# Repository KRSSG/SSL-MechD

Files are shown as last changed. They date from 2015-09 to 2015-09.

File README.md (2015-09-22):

# SSL-MechD
Mechanical Design of Robocup SSL Robots designed by KRSSG, IIT Kharagpur

##SSL v1.0

##SSL v2.0

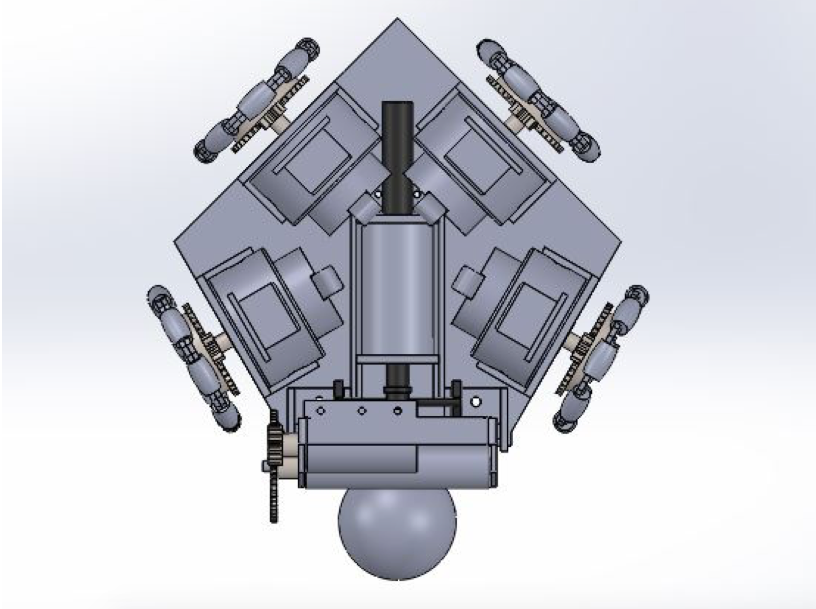
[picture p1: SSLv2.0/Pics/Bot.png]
SSL v2.0


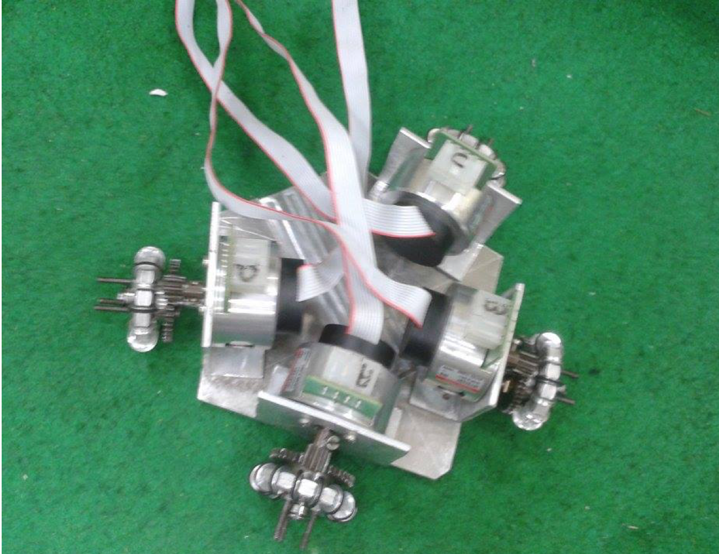
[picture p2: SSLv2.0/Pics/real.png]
SSL Robot


###Locomotion System
The locomotion system is a four wheel drive with 2 wheels inclined at 90° and the other two inclined at 120° to provide space for dribbler and kicker mechanism. The bot has a single centre of rotation and it comes well within the 18 cm diameter following the rules of Small Sized League Robocup competition (SSL). 
#####Wheels
Omni wheels are used which can move in either direction. There are 8 small sub wheels which allows the wheel to move perpendicularly.
#####Gears
Spur gears are used between wheels and motors. 
#####Motors
The motor used for driving is Maxon EC 45.

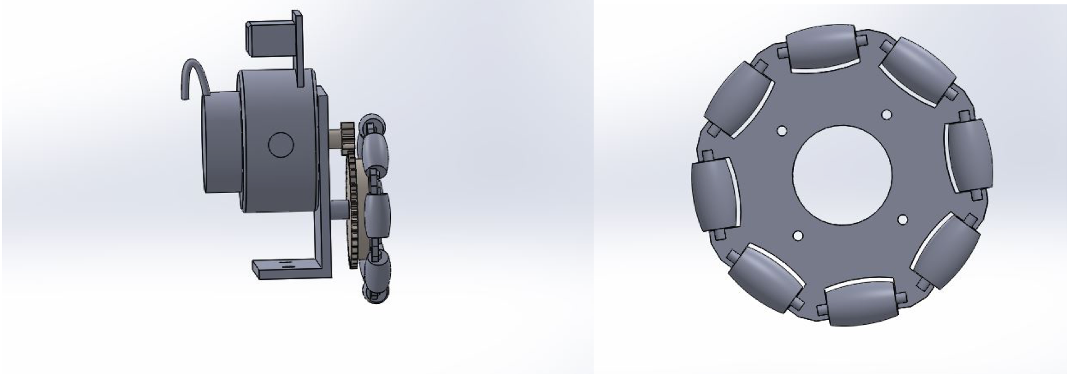
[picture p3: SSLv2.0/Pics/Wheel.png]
Wheel


###Dribbling Mechanism

A circular dribbler made of Aluminium is used. Dribbler bar is directly driven by a brushless Maxon EC16 (16W) motor through the gears with a gear ratio of 4:1. 
To stop the ball from recoiling on impact spring is used to dissipate its kinetic energy to ensure a maximum of ball handling. Further, rubber pad will be used as dampener.
 
According to the rules, geometrical design of this system is in a way that it should not consist more than 20% of the ball. Furthermore, the ball should stick entirely to the robot during the movement. So our Dribbler holds up to 20% of the ball when receiving a pass, and somewhat less than when the ball is at rest or during normal dribbling.

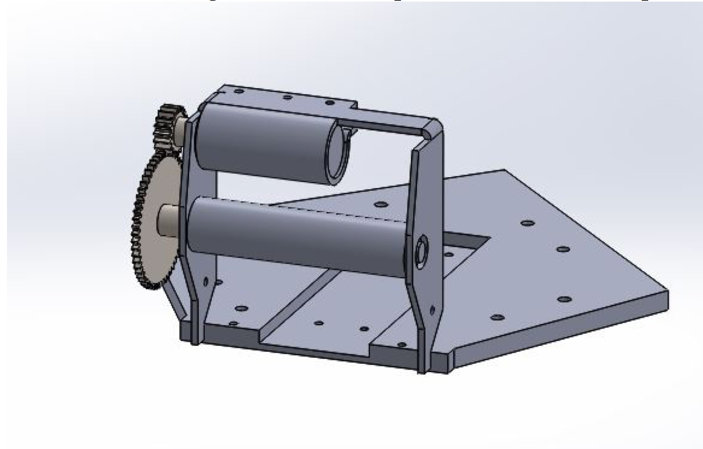
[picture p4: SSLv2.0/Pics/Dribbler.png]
Dribbler


###Kicker System
The shooting mechanism is works on the principle of inductive resistance. When electricity passes through a solenoid, a magnetic field is created. As the number of cycles or amount of electricity is increased, the magnetic field gets stronger. The magnetic materials can be absorbed or repelled through a magnetic field.
The available solenoids are flat and wide and have low voltage, they have a fairly slow movement, so they are not suitable for shooting mechanisms. The solenoids for shooting should be fast and should require a small space. So cylindrical solenoids are used which provides more power and cover much smaller area.

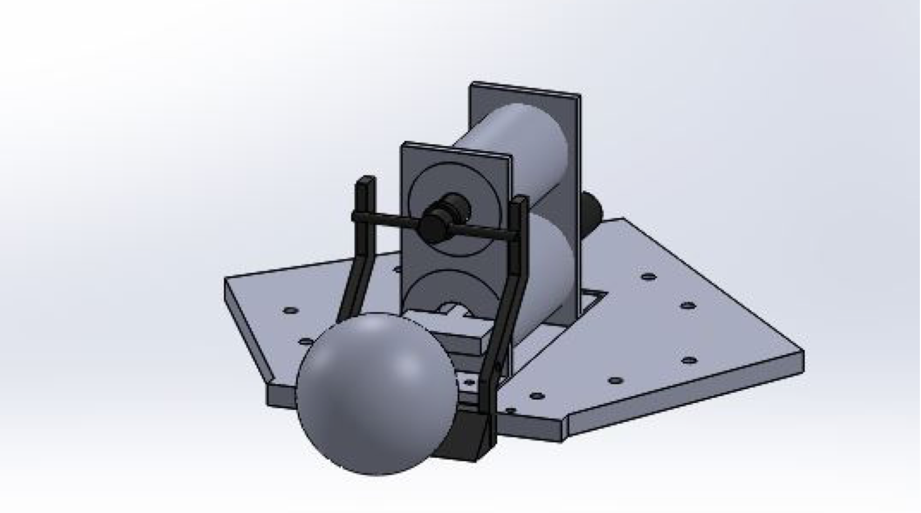
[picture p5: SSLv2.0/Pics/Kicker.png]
Kicker


####Straight Kicker   
Dimensions:
* Solenoid: 	Push type                                   
  * Outer diameter =30mm  
  * Inner diameter =12mm            
  * Length =40mm
  * Wire gauge: 24 AWG               
  * No. of turns=450
* Plunger:
  * Diameter =11mm                       
  * Length=50mm
  * Material: iron
* Striker: 	T shaped with square cross section
* Material: Aluminium

At 400 V charged capacitor & stroke length of 17mm was kept the flat kicker kicked ball at an average speed of 11.25m/s.

####Chip Kicker
Dimensions:
* Solenoid: 	pull type
  * Outer diameter = 26mm
  * Inner diameter = 9mm              
  * Length=40mm
  * Wire gauge: 24 AWG               
  * No. of turns=300
* Plunger
  * Diameter = 8mm                                 
  * Length=50mm
* Material: iron
The chip kicker didn’t gave satisfactory result and is still under development.

##SSL v2.1

##Straight Kicker
Straight kicker consists of solenoid and plunger. Plunger is the one that hits the ball. 

###Solenoid
The frame of solenoid is made of 6061-Aluminium alloy and is cylindrical in shape with an inner diameter of 11.4mm and an outer diameter of12.5mm. Its length is 44mm and thickness is 0.55mm. The wires wound around it are 24 AWG wires and the number of turns is approximately 400. We assume that a constant current of 40 A flows in it throughout its application time.
###Plunger
Straight kicker consists of a custom made plunger with magnetic material (pure iron) in the middle and aluminium upon the remaining length. The length of the iron part is 45mm.The diameter of plunger is 11mm.
 
The Dynamic Analysis of a solenoid which when fed by constant current was done using MATLAB 2013a, FEMM 4.2 and ADAMS software’s.

####Approach
The initial position of plunger in the solenoid across the two cross sections was created using FEMM 4.2. Then, the plunger was made to move a little distance (about 1 mm) into the solenoid in each iteration on MATLAB. In each iteration the force was calculated in the plunger and stored in an array f while its distance from its initial position was stored in x. The iterations were carried on till the plunger reached its final position (here after 40 iterations). The force was calculated in each iteration. Finally the plot of force vs distance was generated. The area of the enclosed in the graph is supposed to give the energy supplied by the solenoid to the plunger.

##Chip Kicker

The Dynamic Analysis of a solenoid which when fed by constant current was done using MATLAB 2013a and FEMM 4.2 softwares.

2 plunger designs were used. One with a thickness of 3.52 mm and length of 64mm (Plunger 1) and the other with a thickness of 2.67 mm and length of 70.75 mm (Plunger 2). Both plungers are 33.8 mm wide.

###Approach
Using FEMM 4.2 software,image initial position of plunger image was created in the solenoid across the two cross sections. Then using a code in MATLAB the plunger was made to move a distance of 1 mm into the solenoid in each iteration. In each iteration the force was calculated in the plunger and stored in an array f while its distance from its initial position was stored in x. The iterations were carried on till the plunger reached it’s final position (here after 33 iterations). The force was calculated on both the cross sections and added. Finally the plot of force vs distance was generated. The area of the enclosed in the graph gave us the energy supplied by the solenoid to the plunger.

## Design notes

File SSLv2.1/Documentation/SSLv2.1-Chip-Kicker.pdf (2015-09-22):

## Dynamic Analysis of a solenoid of chip kicker used in testing

The Dynamic Analysis of a solenoid which when fed by constant current was done using MATLAB 2013a and FEMM 4.2 softwares.
Initially we had 2 plunger designs. One with a thickness of 3.52 mm and length of 64mm (Plunger 1) and the other with a thickness of 2.67 mm and length of 70.75 mm (Plunger 2). Both plungers are 33.8 mm wide.
Approach: Using FEMM 4.2 software we created the image initial position of plunger in the solenoid across the two cross sections. Then using a code in MATLAB the plunger was made to move a distance of 1 mm into the solenoid in each iteration. In each iteration the force was calculated in the plunger and stored in an array f while its distance from its initial position was stored in x. The iterations were carried on till the plunger reached it’s final position (here after 33 iterations). The force was calculated on both the cross sections and added. Finally the plot of force vs distance was generated. The area of the enclosed in the graph gave us the energy supplied by the solenoid to the plunger.
Solenoid: The solenoid is fed by constant current of 40 A. Actually the current keeps varying in the solenoid and has a maximum value. Since we don’t know the exact variation of current in the solenoid with respect to time/distance we are assume that a constant current of 40A is passing through it. Its structure is made of 6061-Aluminium alloy which is 1.25 mm thick. The wires are made of 24-AWG Copper and the number of turns is approximately 630. The outer dimensions of solenoid is 44.2mm × 32mm × 15.5mm while the inner hollow space is of dimensions 34.5mm ×32 mm × 4mm. Plunger 1
The thickness of Plunger 1 is 3.52 mm and its complete length is 64 mm. In its initial position the plunger is 4mm inside the

The thickness of Plunger 1 is 3.52 mm and its complete length is 64 mm. In its initial position the plunger is 4mm inside the solenoid and in its final position the plunger has moved a distance of about 32mm inside the solenoid. The plunger is assumed to be made up of pure iron in FEMM simulation.

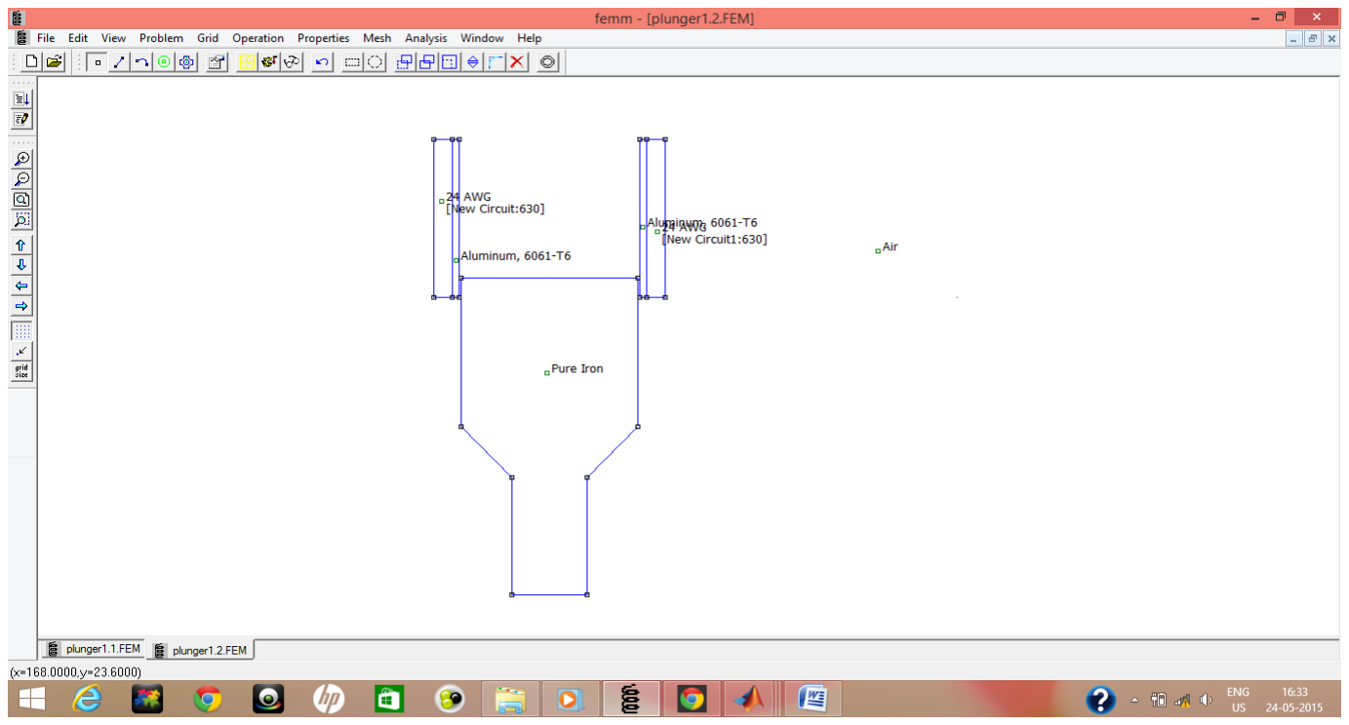
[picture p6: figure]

Across the other cross section the plunger is assumed to be of length 40.3 and we have neglected the thinner tail part and assumed the middle trapezoid as a rectangle.

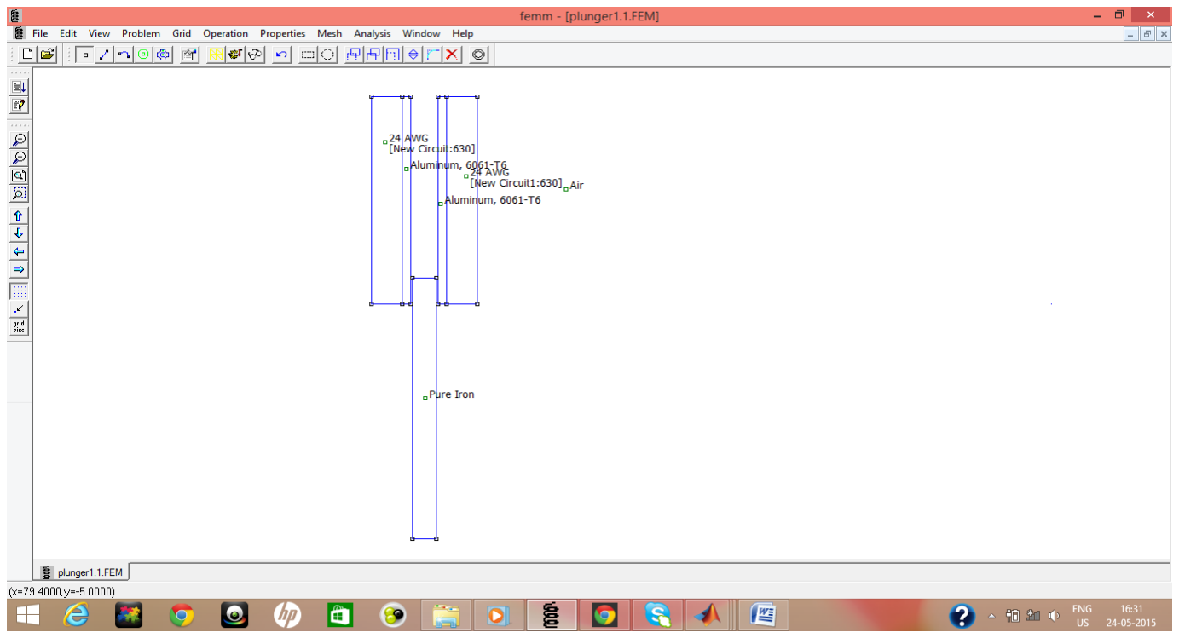
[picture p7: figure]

The boundary in FEMM simulation is kept sufficiently large in comparison with the solenoid dimensions (here a circle of 220 mm radius) .
The following Matlab code was used to generate the graph force vs displacement of the plunger.

openfemm
opendocument('plunger1.1.fem'); mi_saveas('temp.fem');
n=33;
y=zeros(n,1);
f=zeros(n,1);
mi_modifycircprop('New Circuit',1,40);

y=zeros(n,1);
f=zeros(n,1);
mi_modifycircprop('New Circuit',1,40);
for k=1:n
disp(sprintf('iteration %i of %i',k,n)); mi_analyze;
mi_loadsolution;
mo_groupselectblock(1);
y(k)=(k-1);
f(k)= mo_blockintegral(19); disp(sprintf(' force = %f',f(k)));

mi_selectgroup(1);
mi_movetranslate(0,1);
mi_clearselected;
end
closefemm

openfemm
opendocument('plunger1.2.fem'); mi_saveas('temp.fem');
n=33;
mi_modifycircprop('New Circuit',1,40);
for k=1:n
disp(sprintf('iteration %i of %i',k,n)); mi_analyze;
mi_loadsolution;
mo_groupselectblock(1);
y(k)=(k-1);
f(k)= f(k)+ mo_blockintegral(19); disp(sprintf(' force = %f',f(k))); mi_selectgroup(1);
mi_movetranslate(0,1);
mi_clearselected;
end

plot(y,f)
xlabel('Displacement, mm'); ylabel('Force, N');
title('Plunger Force vs. Displacement'); a = trapz(y,f);
disp(sprintf('Area = %f',a));
closefemm

The following graph is generated. The area is calculated by trapz() function which uses trapezoidal method to find the area under the curve.

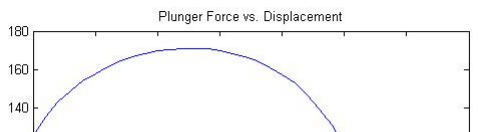
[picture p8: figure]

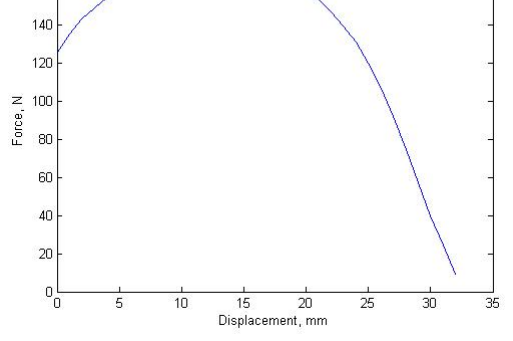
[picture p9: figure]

The area enclosed by the graph = 4386.895186 units
Thus Energy = 4.387 Joules (approx).
Plunger 2
The thickness of Plunger 2 is 2.67 mm and its complete length is 70.75 mm. In its initial position the plunger is 9mm inside the solenoid and in its final position the plunger has moved a distance of about 26 mm inside the solenoid. The plunger is assumed to be made up of pure iron in FEMM simulation.

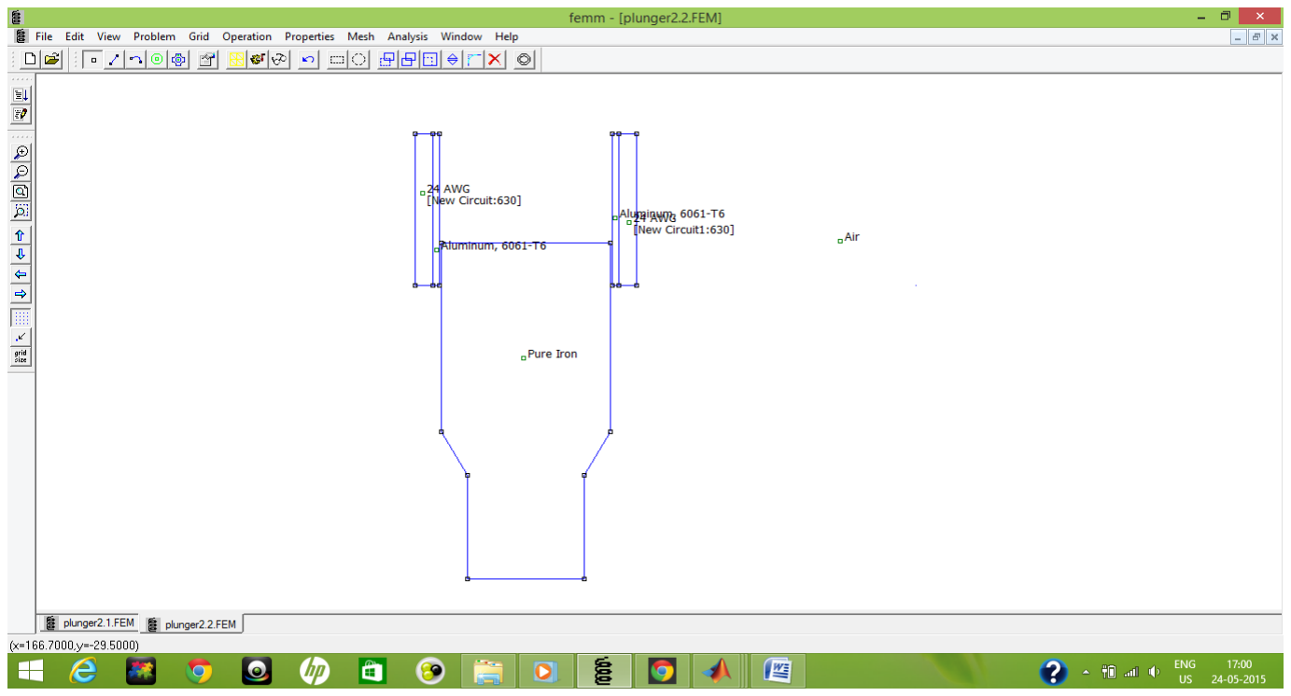
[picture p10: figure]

Across the other cross section the plunger is assumed to be of length 46.25 and we have neglected the thinner tail part and assumed the middle trapezoid as a rectangle.

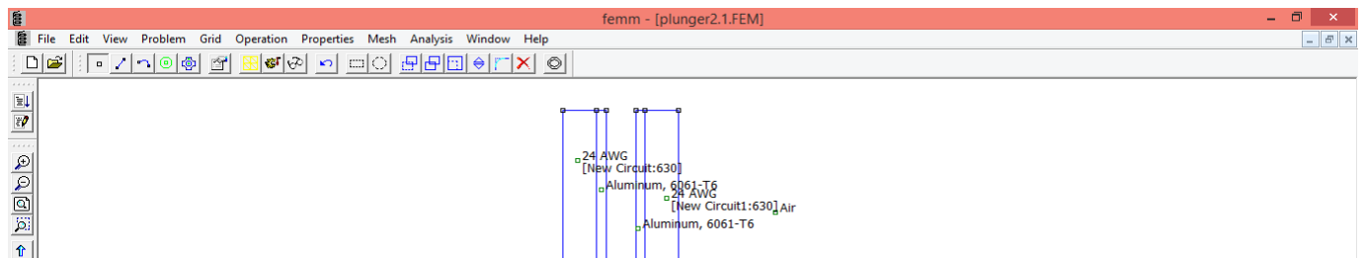
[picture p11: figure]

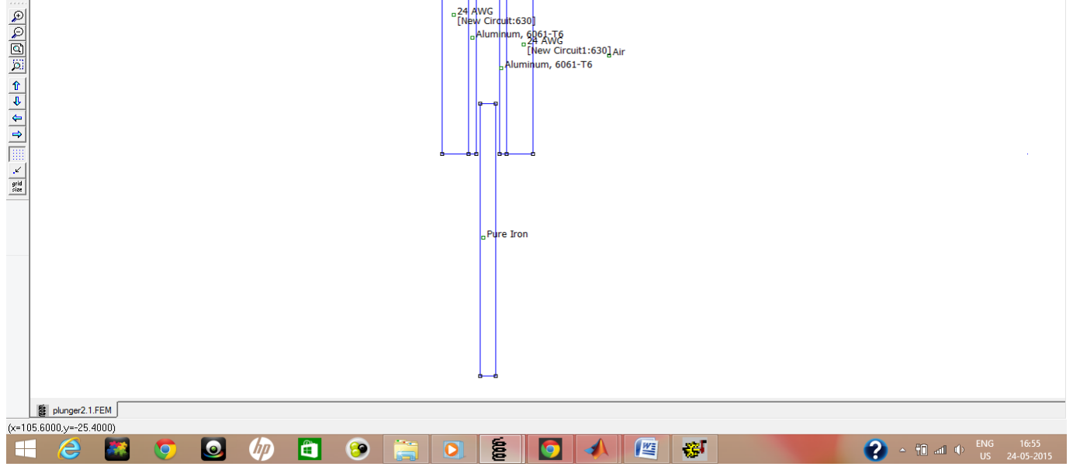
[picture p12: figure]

The boundary in FEMM simulation is kept sufficiently large in comparison with the solenoid dimensions (here a circle of 220 mm radius) .
The following Matlab code was used to generate the graph force vs displacement of the plunger.

openfemm
opendocument('plunger2.1.fem'); mi_saveas('temp.fem');
n=28;
y=zeros(n,1);
f=zeros(n,1);

for k=1:n
disp(sprintf('iteration %i of %i',k,n)); mi_analyze;
mi_loadsolution;
mo_groupselectblock(1);
y(k)=(k-1);
f(k)= mo_blockintegral(19); disp(sprintf(' force = %f',f(k))); mi_modifycircprop('New Circuit',1,40); mi_selectgroup(1);
mi_movetranslate(0,1);
mi_clearselected;
end
closefemm

openfemm
opendocument('plunger2.2.fem'); mi_saveas('temp.fem');
n=28;
for k=1:n
disp(sprintf('iteration %i of %i',k,n)); mi_analyze;
mi_loadsolution;
mo_groupselectblock(1);
y(k)=(k-1);
f(k)= f(k)+ mo_blockintegral(19);

y(k)=(k-1);
f(k)= f(k)+ mo_blockintegral(19);

disp(sprintf(' force = %f at distance %f',f(k),y(k)));
mi_modifycircprop('New Circuit',1,40); mi_selectgroup(1);
mi_movetranslate(0,1);
mi_clearselected;
end

plot(y,f)
xlabel('Displacement, mm'); ylabel('Force, N');
title('Plunger Force vs. Displacement'); a = trapz(y,f);
disp(sprintf('Area = %f',a));
closefemm

The following graph is generated. The area is calculated by trapz() function which uses trapezoidal method to find the area under the curve.

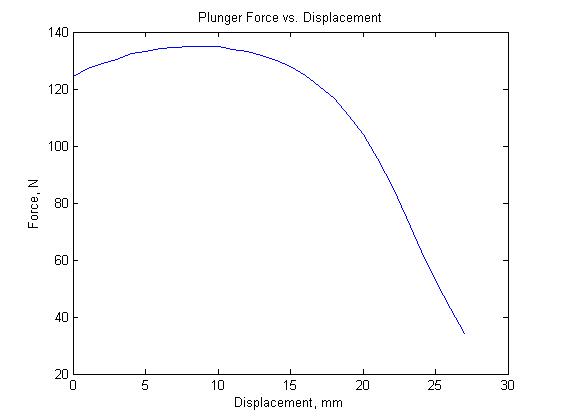
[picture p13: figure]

The area enclosed by the graph = 3053.359648units

Thus Energy = 3.053 Joules (approx).
Conclusion: Plunger 1 (length 64 mm and thickness 3.52 mm) is observed to provide more energy(4.387 J ) than Plunger 2 ( length 70.75 mm and thickness 2.67 mm) which provides 3.053 J.

Plunger 2 ( length 70.75 mm and thickness 2.67 mm) which provides 3.053 J.
Overall its observed that a plunger with greater length and thickness keeping width constant for the same solenoid and current possess more energy.

## Testing of chip kicker on a wooden base

The chip kicker was tested on a wooden base. We used adams software to run the simulation .The range and height of the ball was calculated by the adams software based on force equation which was generated by matlab and fed into adams. The kicker setup was replicated and tested on a wooden base to test wether the original results matched with the results we got from the software.
The trajectory of the ball which we got in the simulation:

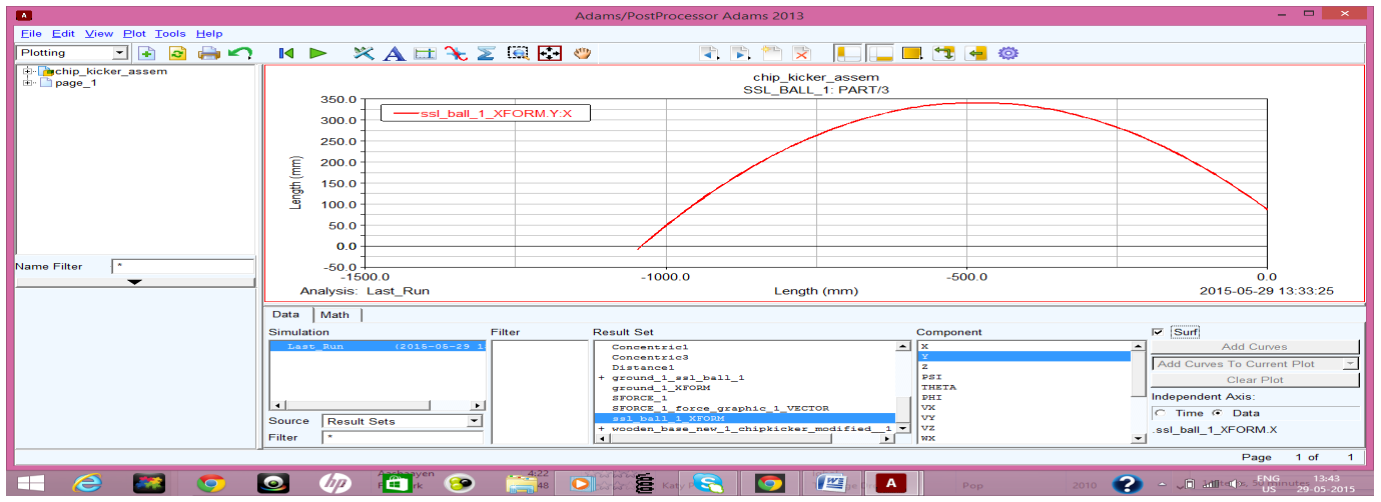
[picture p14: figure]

However in this plot we have applied the force in negative x axis so the ball is moving towards the negative x-direction i.e. the all moves from a point with x co-ordinates 0.0 to a point with x co ordinates about -1100.
From this plot we get that :
Distance which the ball travels in horizontal direction: 1.1 m (approx.)
Maximum height attained by the ball : 0.35 m (approx.)

The actual results which we got by testing the chip kicker on the wooden base :
Distance which the ball travels in horizontal direction: 1.3 m

the wooden base :
Distance which the ball travels in horizontal direction: 1.3 m Maximum height attained by the ball : 0.27 m

Hence the actual results and the observed results are quite similar. The differences are due to several assumptions we have taken during the simulation.

# Dynamic analysis of solenoid for chip kicker in ssl bot

The solenoid and plunger which we used for testing was different from the one which we used in the actual bot.
In addition to the above procedures we also used ADAMS software to simulate the chip kicker and to predict the trajectory of the ball. For using ADAMS we have to import the solid works model of the chip kicker along with all the contact forces acting on the various components of the model. Then using MATLAB we generate the best fit polynomial of force as a function of x which is the distance moved by the plunger. MATLAB generates at max. a 10 degree polynomial for the estimation of a curve. We use this polynomial and apply it to the plunger and then find the trajectory of the ball. Apart from the above arrangement we are also using a shell which is made of steel/iron. It is found that using a shell significantly increases the energy of the solenoid. The shell which we are using is 2mm thick.
Solenoid: The solenoid is fed by constant current of 40 A. Actually the current keeps varying in the solenoid and has a maximum value. Since we don’t know the exact variation of current in the solenoid with respect to time/distance we are assume that a constant current of 40A is passing through it. Its structure is made of 6061-Aluminium alloy which is 1.25 mm thick. The wires are made of 24-AWG Copper and the number of turns is approximately 400. The outer dimensions of solenoid is 46mm × 43mm × 12mm while the inner hollow space is of dimensions 46mm ×38 mm × 4mm. There is also a of turns is approximately 400. The outer dimensions of solenoid is 46mm × 43mm × 12mm while the inner hollow space is of dimensions 46mm ×38 mm × 4mm. There is also a 2mm thick steel/iron shell surrounding the solenoid.
Plunger: The plunger is made of iron. It is assumed to be a cuboid though it is not. It’s dimensions are 52mm × 37mm × 3.8mm.
The FEMM files :
In its initial position the plunger is 4mm inside the solenoid and in its final position the plunger has moved a distance of 40 mm inside the solenoid.
The boundary in FEMM simulation is kept sufficiently large in comparison with the solenoid dimensions (here a circle of 220 mm radius) .

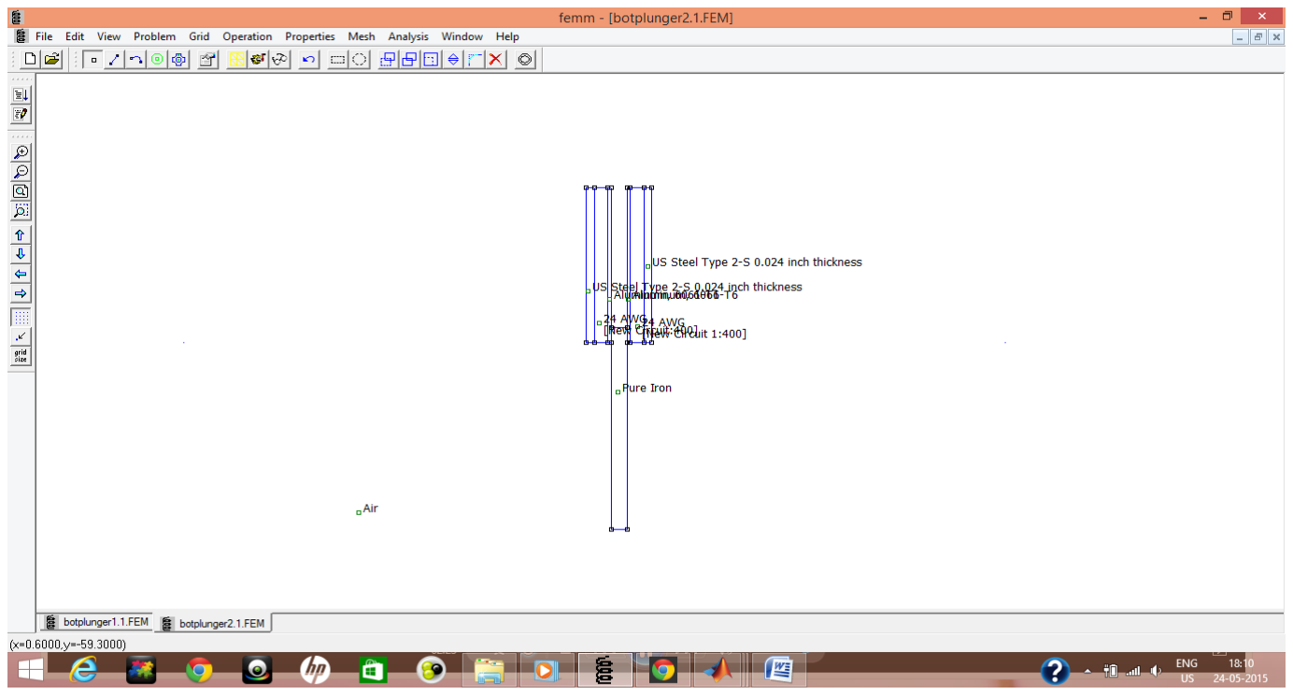
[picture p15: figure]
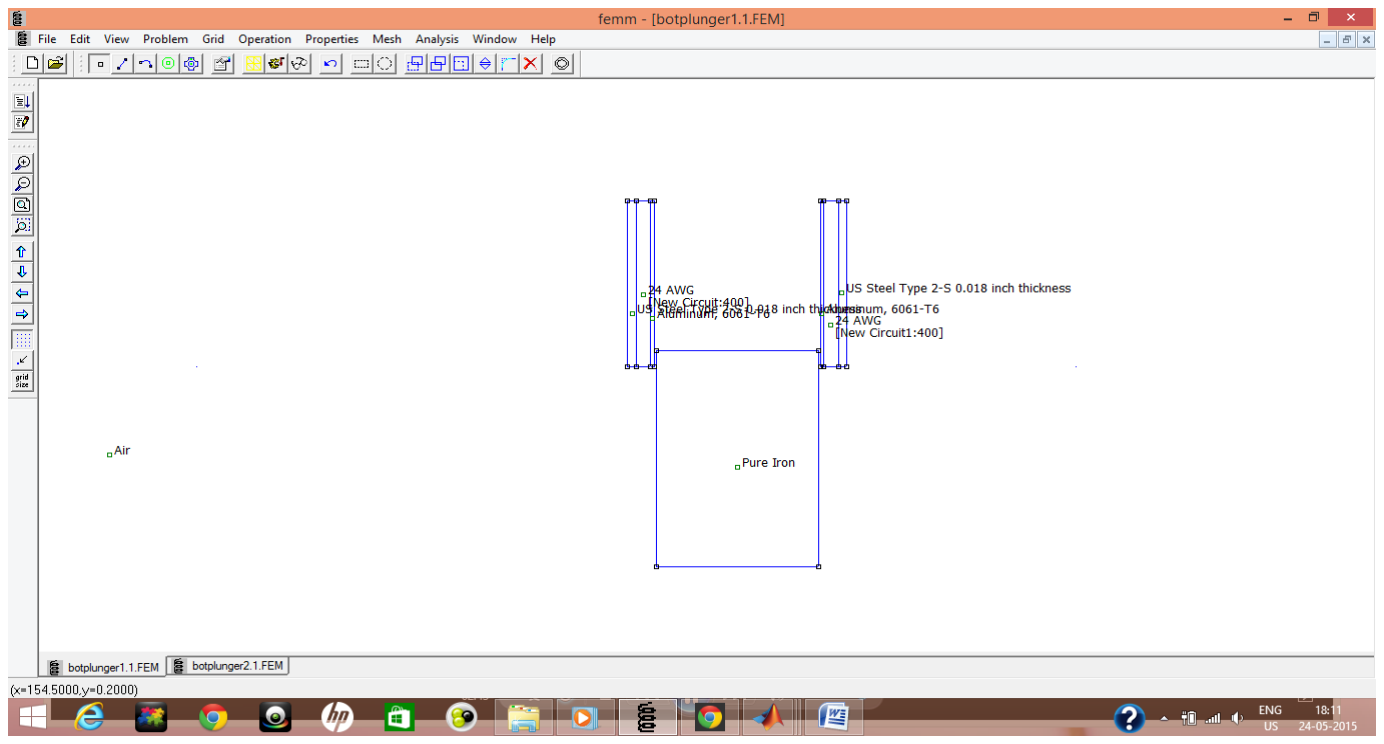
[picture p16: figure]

The MATLAB code used is :

openfemm

The MATLAB code used is :

openfemm

opendocument('botplunger1.1.fem');% the file is opened mi_saveas('temp.fem');% a temperory file is formed ..all the changes will be reflected only in this file
n=44;% number of iterations
mi_modifycircprop('New Circuit',1,40);% the current in 'New Circuit'is 40 A
y=zeros(n,1); % y i.e the distance array is initialised f=zeros(n,1);% f i.e the force array is initialised
for k=1:n % the for loop starts
disp(sprintf('iteration %i of %i',k,n));
mi_analyze;
mi_loadsolution;% meshing and analyszing has been done mo_groupselectblock(1);% group 1 i.e plunger is selected y(k)=(k-1);
f(k)=mo_blockintegral(19);% the force in y direction on the selected group
disp(sprintf(' force = %f',f(k)));
mi_selectgroup(1);% group 1 i.e plunger is selected mi_movetranslate(0,1);% group 1 is moved upwards by 1 mm mi_clearselected; % group 1 is cleared
end % for loop ends
closefemm
openfemm

opendocument('botplunger2.1.fem'); % new femm file is opened mi_saveas('temp.fem');
n=44;
mi_modifycircprop('New Circuit',1,40);
for k=1:n
disp(sprintf('iteration %i of %i',k,n)); mi_analyze;
mi_loadsolution;
mo_groupselectblock(1);
y(k)=(k-1);
f(k)=f(k) + mo_blockintegral(19); disp(sprintf(' force = %f',f(k))); mi_selectgroup(1);
mi_movetranslate(0,1);
mi_clearselected;
end
plot(y,f) % a plot is drawn between y i.e distance and f i.e force
xlabel('Displacement, mm'); % x axis is labeled ylabel('Force, N'); % y axis is labeled
title('Plunger Force vs. Displacement');
a = trapz(y,f); % the area of the graph is calculated and shown

disp(sprintf('Area = %f',a));
closefemm

The graph generated :

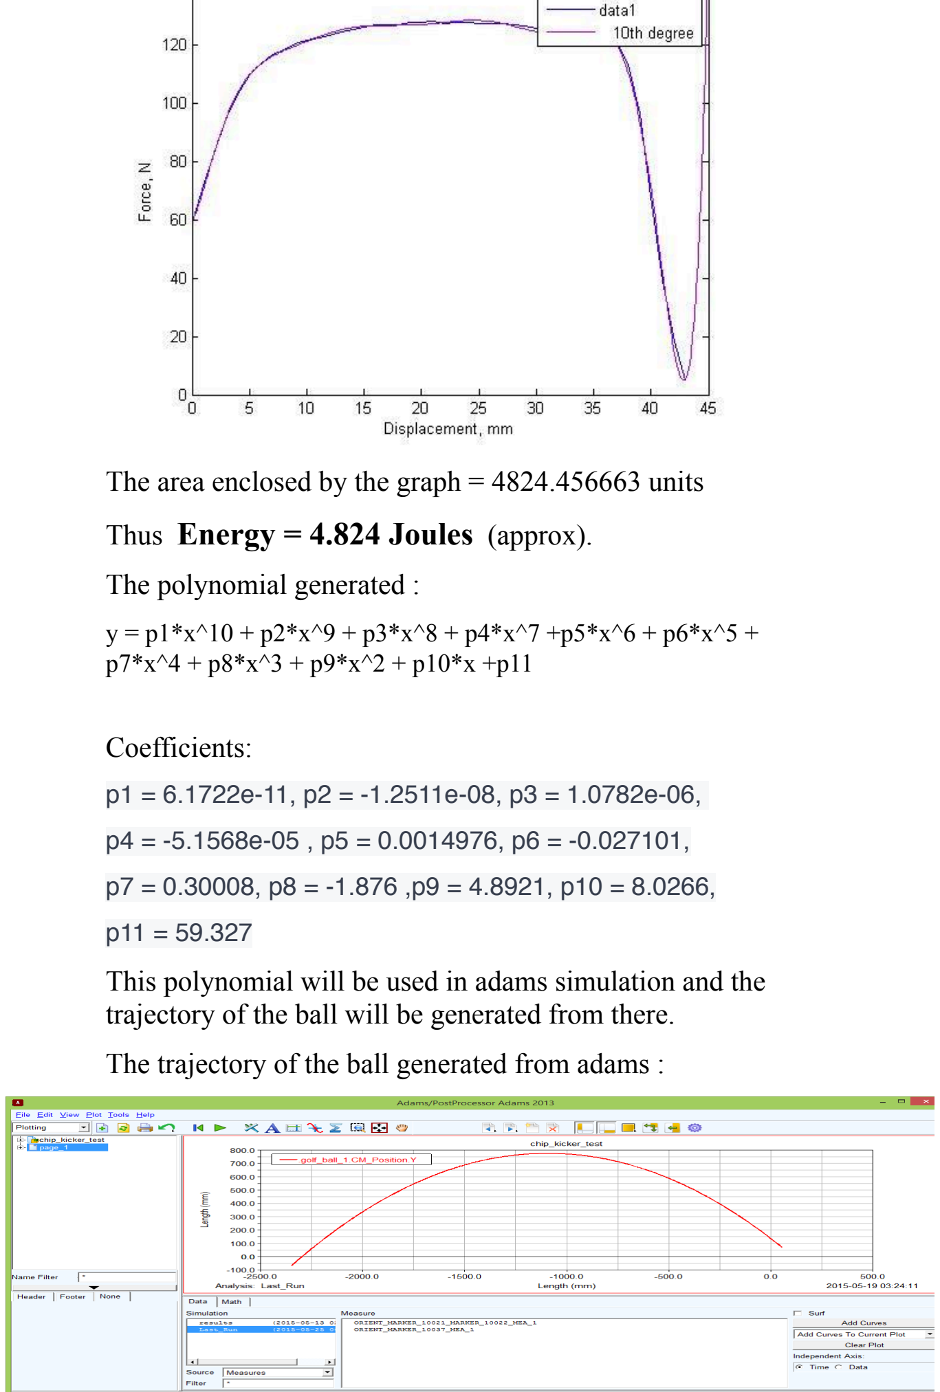
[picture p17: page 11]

The area enclosed by the graph = 4824.456663 units Thus Energy = 4.824 Joules (approx).
The polynomial generated :

y = p1*x^10 + p2*x^9 + p3*x^8 + p4*x^7 +p5*x^6 + p6*x^5 + p7*x^4 + p8*x^3 + p9*x^2 + p10*x +p11

Coefficients:

p1 = 6.1722e-11, p2 = -1.2511e-08, p3 = 1.0782e-06,

p4 = -5.1568e-05 , p5 = 0.0014976, p6 = -0.027101,

p7 = 0.30008, p8 = -1.876 ,p9 = 4.8921, p10 = 8.0266,

p11 = 59.327
This polynomial will be used in adams simulation and the trajectory of the ball will be generated from there.
The trajectory of the ball generated from adams :

However in this plot we have applied the force in negative x axis so the ball is moving towards the negative x-direction i.e. the all moves from a point with x co-ordinates of about 10 to a point with x co ordinates about -2300.
From this plot we get that :
Distance which the ball travels in horizontal direction: 2.3 m (approx.)
Maximum height attained by the ball : 0.75-0.8 m (approx.) However in our calculations we have taken a whole lot of assumptions and the actual results may differ slightly from the calculated results.
The errors may be due to following assumptions:
- The current is kept constant at 40A. But actually it varies a lot.
- All type of frictional forces acting between various components of our model has been neglected.
- Proper and perfect alignment of the plunger, chip kicker and the ball is not always possible.

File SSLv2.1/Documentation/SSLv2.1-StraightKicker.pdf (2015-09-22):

STRAIGHT KICKER

Straight kicker consists of solenoid and plunger. Plunger is the one that hits the ball.

Solenoid:
The frame of solenoid is made of 6061-Aluminium alloy and is cylindrical in shape with an inner diameter of 11.4mm and an outer diameter of12.5mm. Its length is 44mm and thickness is 0.55mm. The wires wound around it are 24 AWG wires and the number of turns is approximately 400. We assume that a constant current of 40 A flows in it throughout its application time.
Plunger:
Straight kicker consists of a custom made plunger with magnetic material (pure iron) in the middle and aluminium upon the remaining length. The length of the iron part is 45mm.The diameter of plunger is 11mm.

The Dynamic Analysis of a solenoid which when fed by constant current was done using MATLAB 2013a, FEMM 4.2 and ADAMS software’s. Approach:
Using FEMM 4.2 software we created the image initial position of plunger in the solenoid across the two cross sections. Then using a code in MATLAB the plunger was made to move a little distance (about 1 mm) into the solenoid in each iteration. In each iteration the force was calculated in the plunger and stored in an array f while its distance from its initial position was stored in x. The iterations were carried on till the plunger reached its final position (here after 40 iterations). The force was calculated in each iteration. Finally the plot of force vs distance was generated. The area of the enclosed in the graph gave us the energy supplied by the solenoid to the plunger.
Analysis:
The solenoid and plunger were modelled in Femm 4.2 .

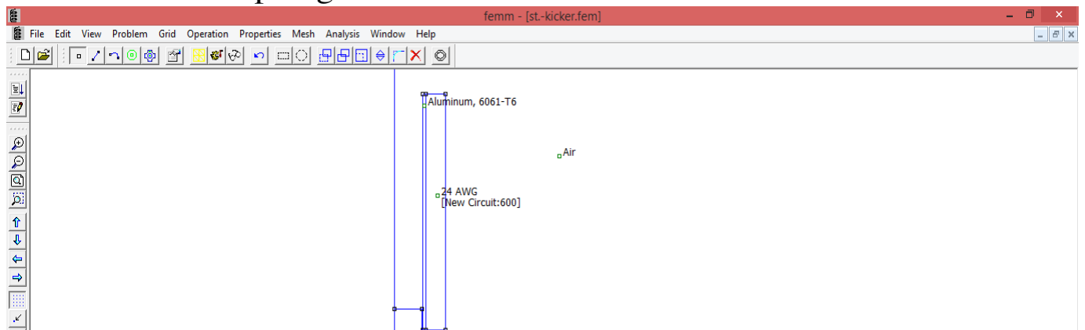
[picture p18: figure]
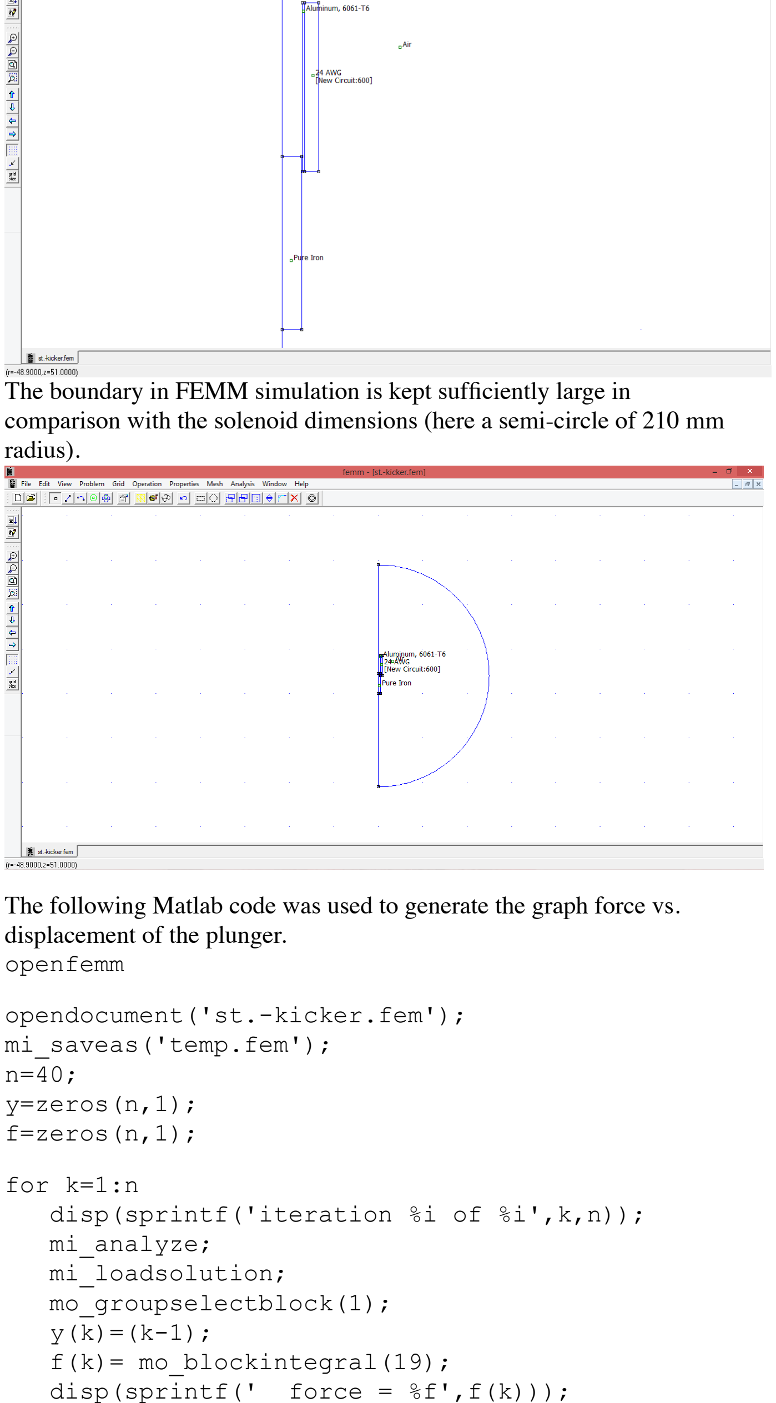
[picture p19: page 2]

The boundary in FEMM simulation is kept sufficiently large in comparison with the solenoid dimensions (here a semi-circle of 210 mm radius).

The following Matlab code was used to generate the graph force vs. displacement of the plunger.
openfemm

opendocument('st.-kicker.fem'); mi_saveas('temp.fem');
n=40;
y=zeros(n,1);
f=zeros(n,1);

for k=1:n
disp(sprintf('iteration %i of %i',k,n)); mi_analyze;
mi_loadsolution;
mo_groupselectblock(1);
y(k)=(k-1);
f(k)= mo_blockintegral(19); disp(sprintf(' force = %f',f(k)));

mi_analyze;
mi_loadsolution;
mo_groupselectblock(1);
y(k)=(k-1);
f(k)= mo_blockintegral(19); disp(sprintf(' force = %f',f(k))); mi_modifycircprop('New Circuit',1,40); mi_selectgroup(1);
mi_movetranslate(0,1);
mi_clearselected;
end

plot(y,f)
xlabel('Displacement, mm'); ylabel('Force, N');
title('Plunger Force vs. Displacement'); a = trapz(y,f);

disp(sprintf('Area = %f',a));
closefemm

The following graph is generated. The area is calculated by trapz () function which uses trapezoidal method to find the area under the curve. The graph gives us relation between force and displacement of plunger. Static Structural Analysis of straight kicker We used ADAMS software to estimate the force while the static structural analysis as done using ANSYS software. Initially a solid works model was created of the straight kicker. The material used was aluminum alloy and cast iron. This model was then used in ADAMS and ANSYS.
The solid works model of the straight kicker :

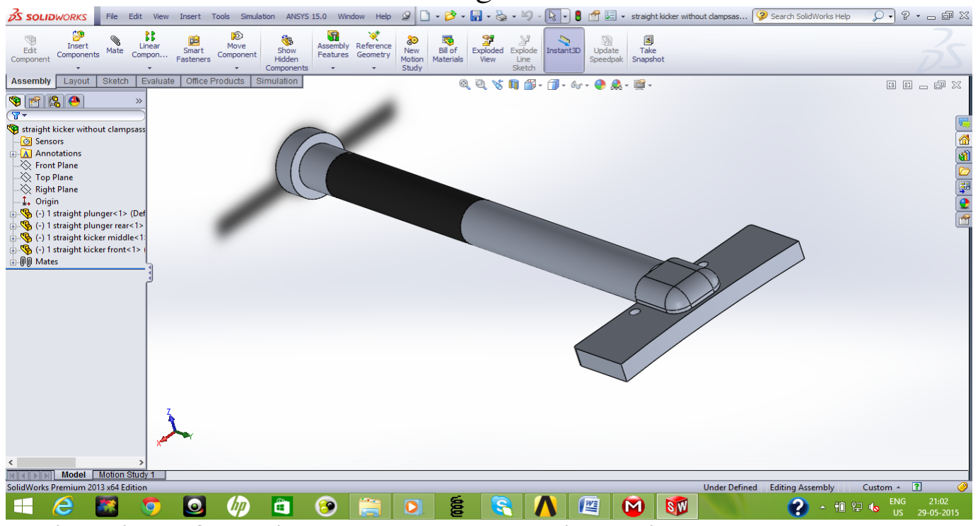
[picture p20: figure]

Estimation of maximum Force on straight kicker:
For the estimation of the maximum force on the kicker during the collision with the ball, ADAMS simulation was used. We got the maximum deceleration of the front part of the kicker and multiplying it with the mass of kicker we got the required force.

Estimation of maximum Force on straight kicker:
For the estimation of the maximum force on the kicker during the collision with the ball, ADAMS simulation was used. We got the maximum deceleration of the front part of the kicker and multiplying it with the mass of kicker we got the required force.

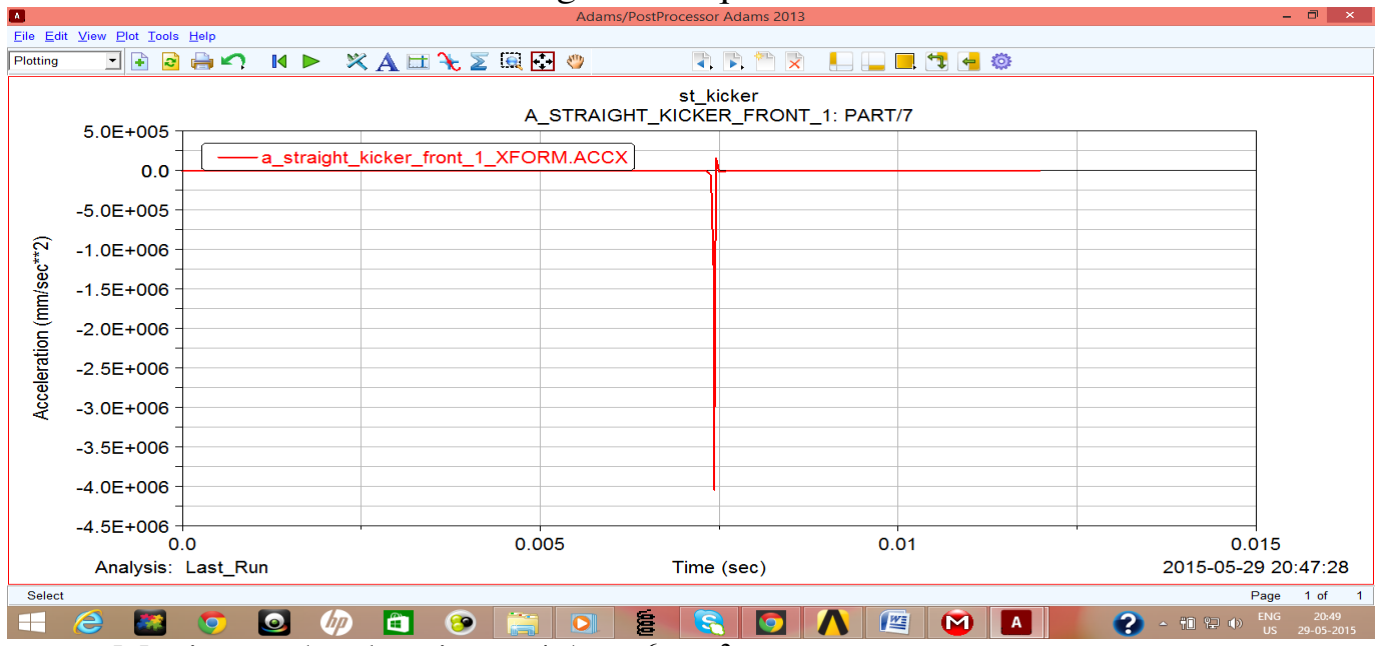
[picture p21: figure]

Maximum deceleration = 4.1×10⁶ ms⁻² (approx)
Mass of the kicker = 64.35 gm
Maximum force = 263835 N
Analysis using ANSYS: In the analysis we are looking at the worst possible case. So we assumed that the entire force is acting on the front face of the kicker while all the side faces are acting as fixed supports. The results of the analysis are as follows:
Total deformation :

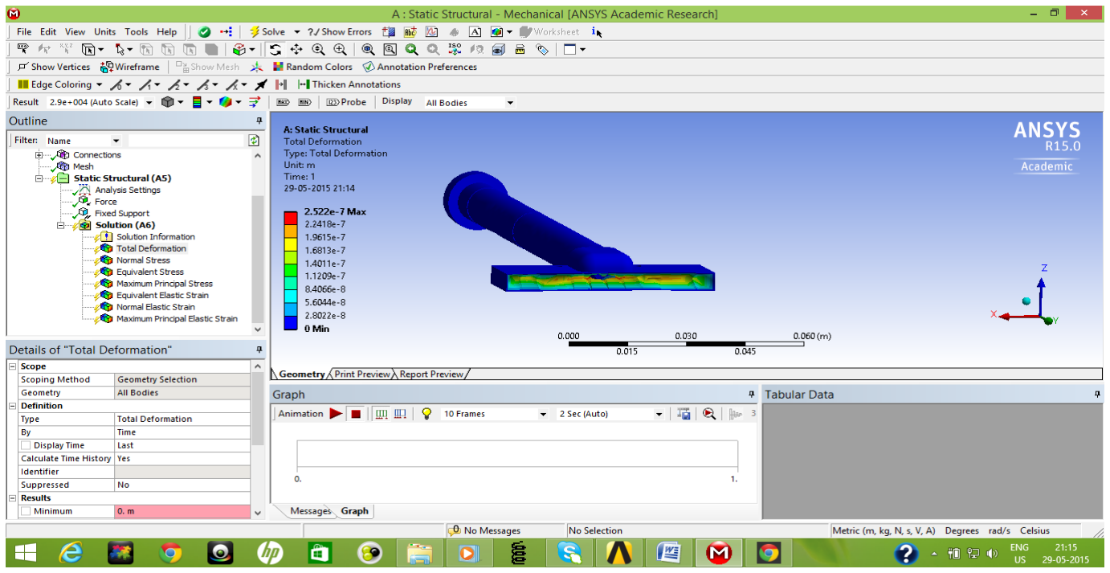
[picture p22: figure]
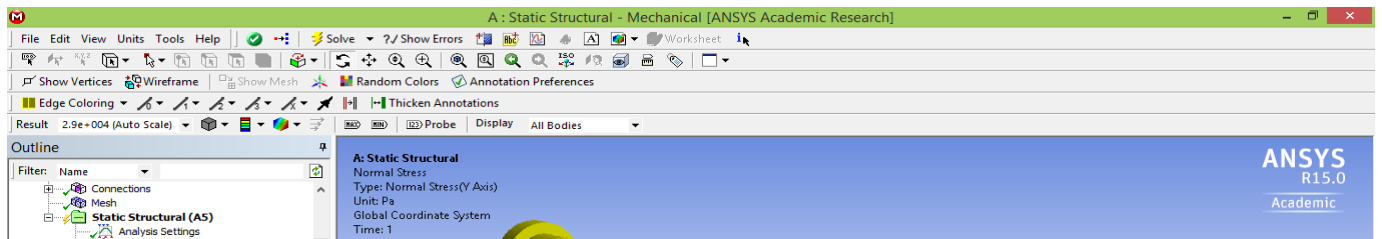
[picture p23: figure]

Normal Stress :

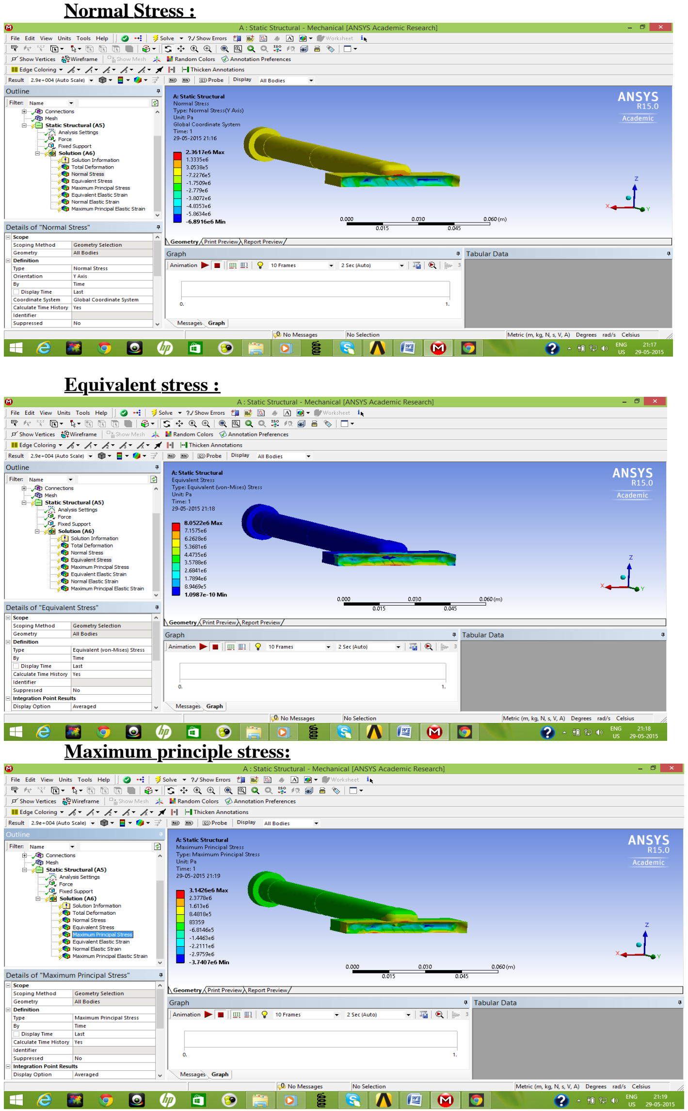
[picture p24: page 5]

Normal Stress :

Equivalent stress :

Maximum principle stress:

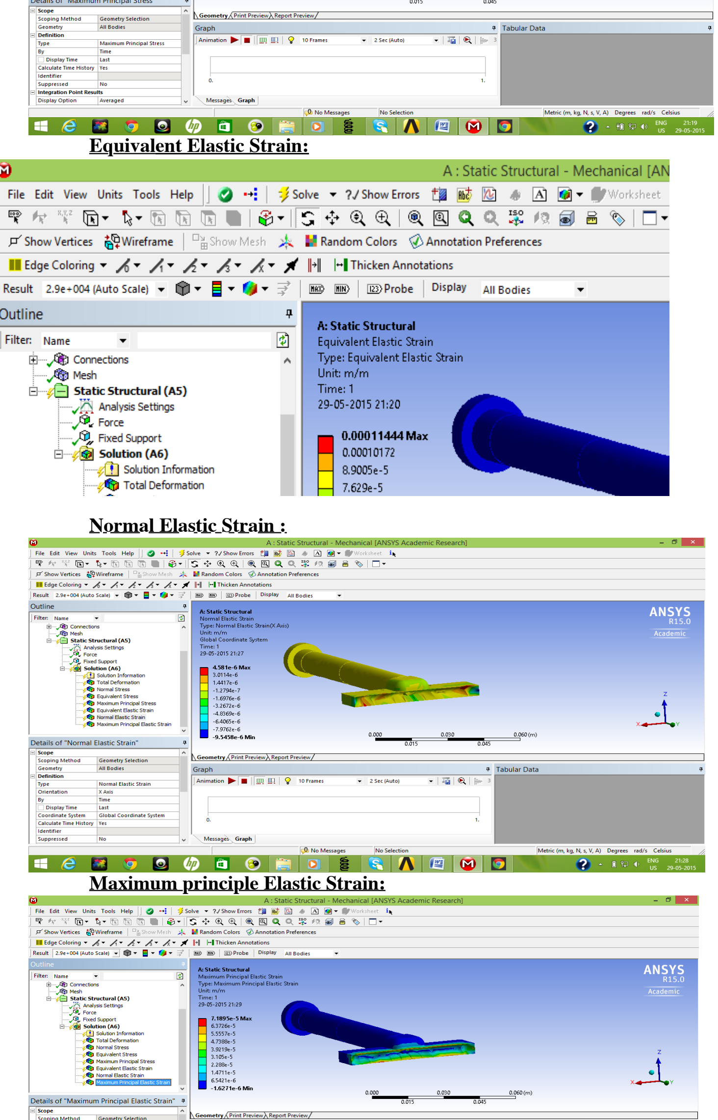
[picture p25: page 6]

Equivalent Elastic Strain:

Normal Elastic Strain :

Maximum principle Elastic Strain:

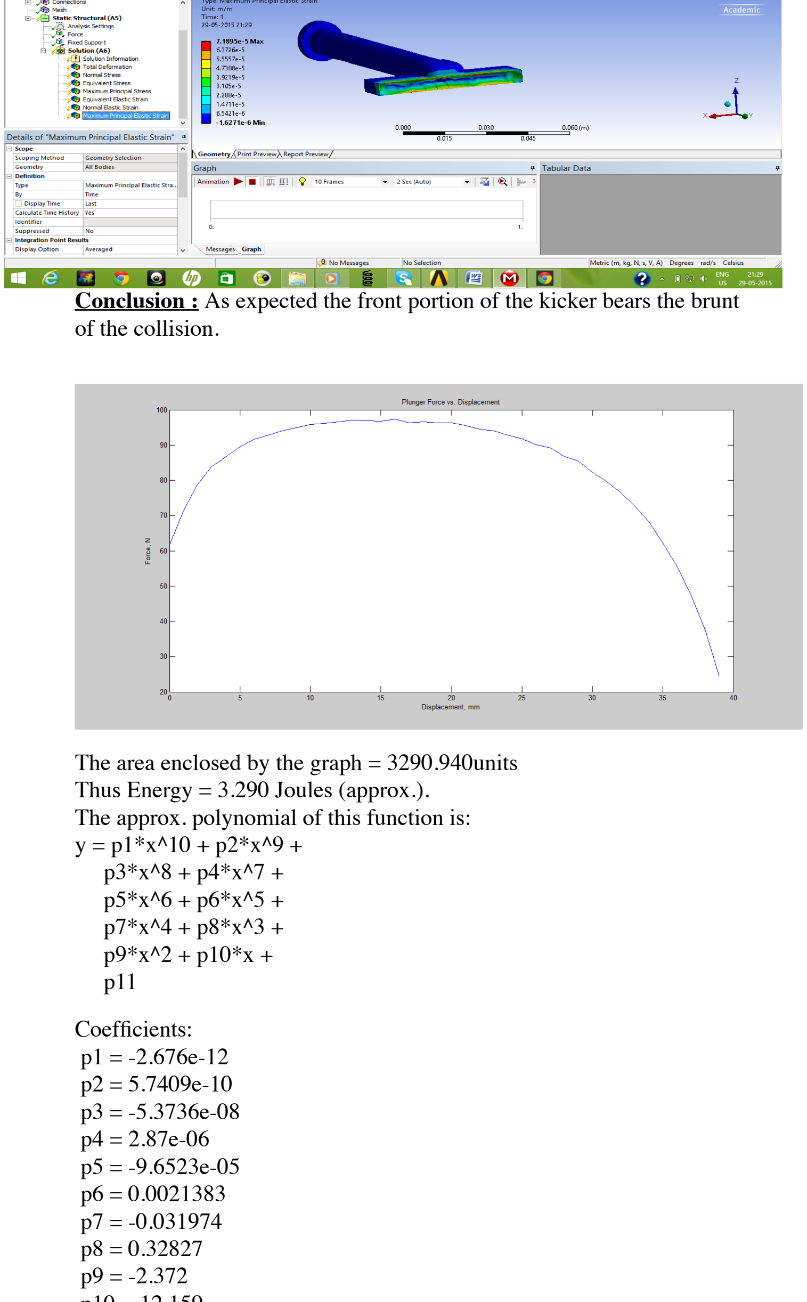
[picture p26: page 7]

Conclusion : As expected the front portion of the kicker bears the brunt of the collision.

The area enclosed by the graph = 3290.940units Thus Energy = 3.290 Joules (approx.).
The approx. polynomial of this function is:
y = p1*x^10 + p2*x^9 +
p3*x^8 + p4*x^7 +
p5*x^6 + p6*x^5 +
p7*x^4 + p8*x^3 +
p9*x^2 + p10*x +
p11

Coefficients:
p1 = -2.676e-12
p2 = 5.7409e-10
p3 = -5.3736e-08
p4 = 2.87e-06
p5 = -9.6523e-05
p6 = 0.0021383
p7 = -0.031974
p8 = 0.32827
p9 = -2.372
p10 = 12.159

p4 = 2.87e-06
p5 = -9.6523e-05
p6 = 0.0021383
p7 = -0.031974
p8 = 0.32827
p9 = -2.372
p10 = 12.159
p11 = 61.585

Later, the polynomial function was feeded in Adams-View software and simulation was done by applying force as obtained in matlab on the plunger.

The graph of speed of ball is :-

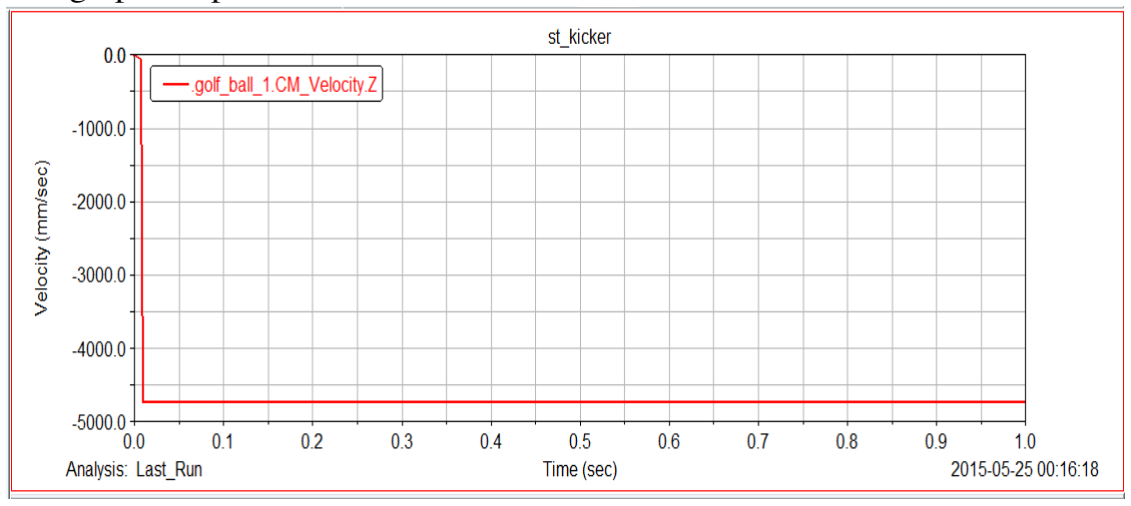
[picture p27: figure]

The simulation gave a speed of ball is about 5m/s.

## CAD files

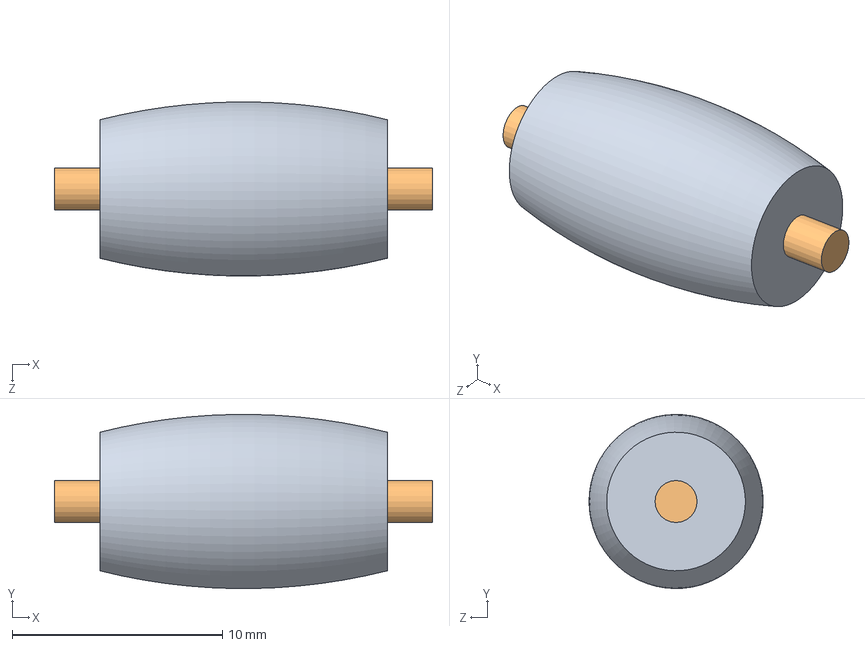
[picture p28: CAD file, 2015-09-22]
SSLv2.0/Omniwheel1/smallassem.SLDASM
18.0 x 8.29 x 8.28 mm
omnismall
smallaxle

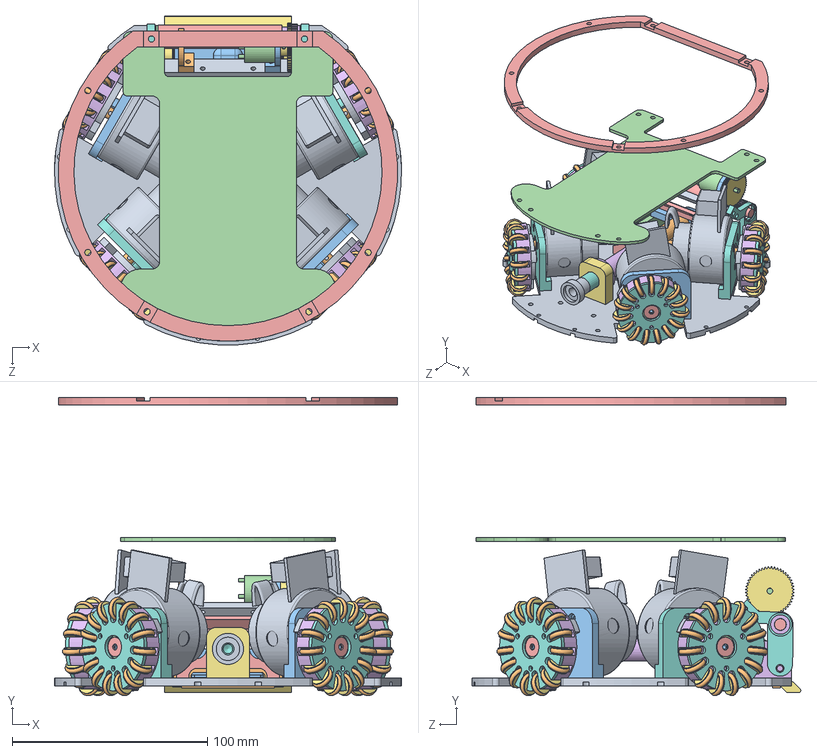
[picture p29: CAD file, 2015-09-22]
SSLv2.1/Designs/ssl robot assembly.SLDASM
177.9 x 153.0 x 168.6 mm
base
1 chip solenoid shell
1 chip plunger
2 chip holder x 2
1 straight front support
1 straight shell
1 straight rear support
1 straight plunger
1 straight plunger rear
1 straight kicker middle
1 straight kicker front
1 side support left
1 dribbler support middle
1 side support right
1 chip kicker
2 dribbler side mount x 2
1 dribbler mount middle
1 motor rear support
1 motor front support
drib gear box
1 dribbler rod
1 rod gear
1 dribbler motor gear
2 motor mount x 2
ssl_motor x 4
4 motor gear x 4
4 main bolt x 4
radial ball bearing_68_am x 4
4 washer x 4
4 back part x 4
60 subwheel x 60
4 front part x 4
4 wheel gear x 4
Sub_o-ring x 60
2 motor mount mirror x 2
1 stack
1 top ring

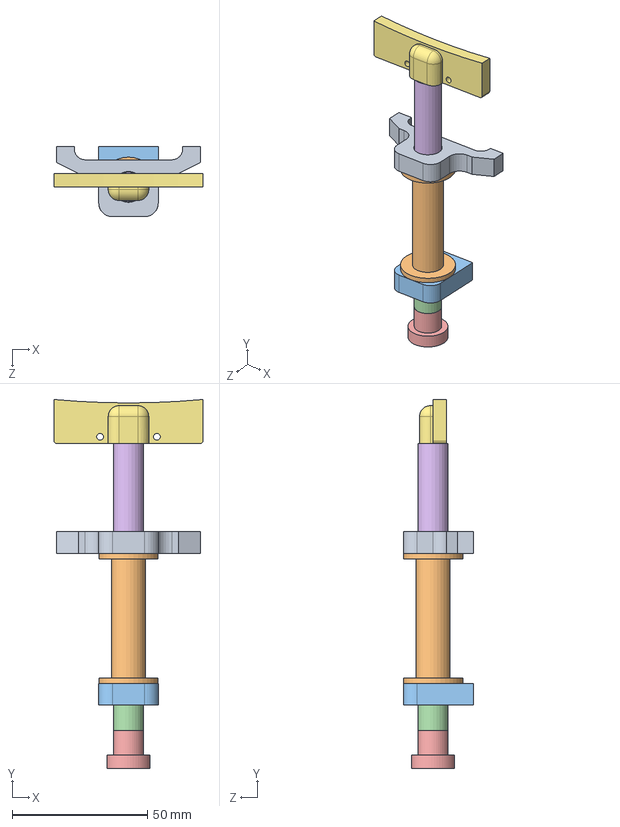
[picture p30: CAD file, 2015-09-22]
SSLv2.1/Designs/straight kicker/straight kicker assembly.SLDASM
55.0 x 136.3 x 26.0 mm
1 straight front support
1 straight shell
1 straight rear support
1 straight plunger
1 straight plunger rear
1 straight kicker middle
1 straight kicker front

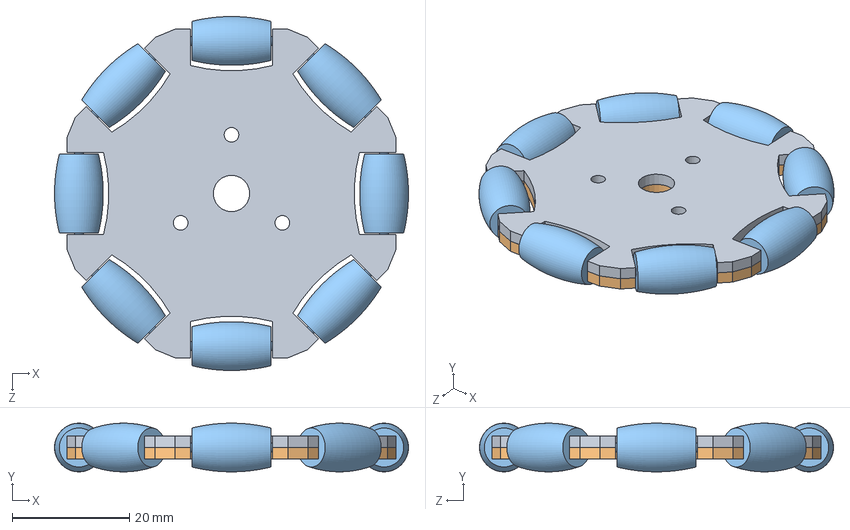
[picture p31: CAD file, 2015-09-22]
SSLv2.0/Omniwheel1/wheelomni.SLDASM
60.3 x 8.30 x 60.3 mm
omnimain
mainmirror
omnismall x 8

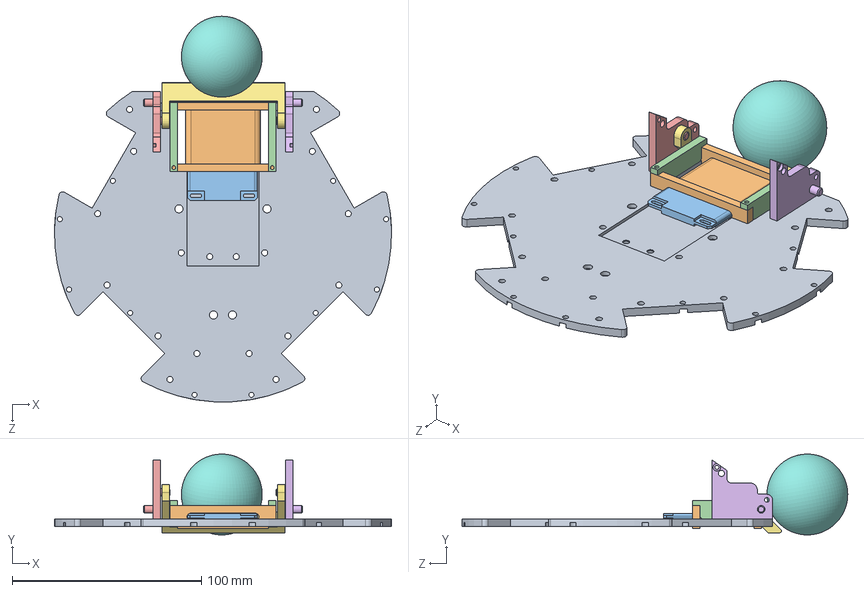
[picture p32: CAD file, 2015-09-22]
SSLv2.1/Designs/chip kicker test.SLDASM
177.9 x 42.7 x 203.6 mm
base
1 chip solenoid shell
1 chip plunger
2 chip holder x 2
1 side support left
1 side support right
1 chip kicker
golf_ball

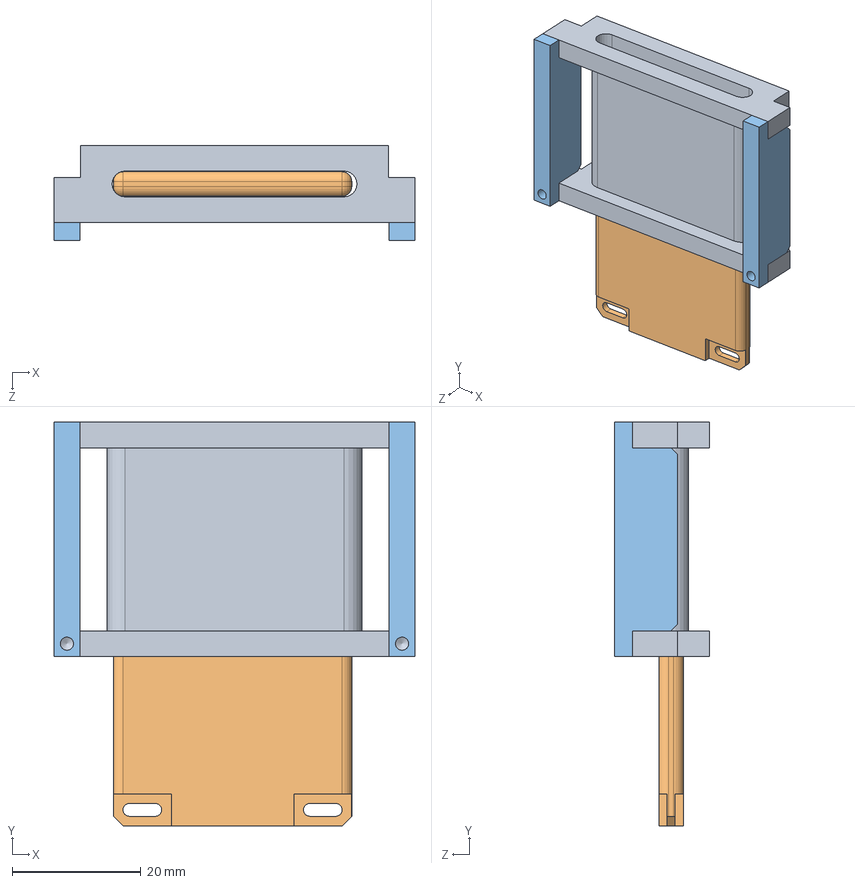
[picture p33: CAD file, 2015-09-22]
SSLv2.1/Designs/chip kicker/chip kicker assembly.SLDASM
56.0 x 62.7 x 14.8 mm
1 chip solenoid shell
1 chip plunger
2 chip holder x 2

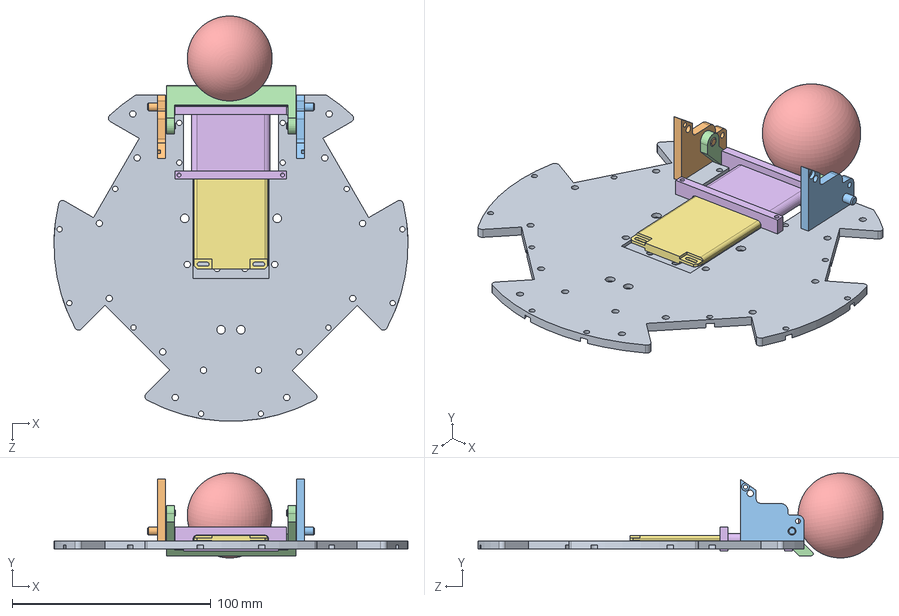
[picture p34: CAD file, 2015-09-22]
SSLv2.1/Designs/chip_kicker_test1.SLDASM
177.9 x 42.7 x 203.6 mm
base
1 side support left
1 side support right
1 chip kicker
golf_ball
1 chip solenoid shell
1 chip plunger

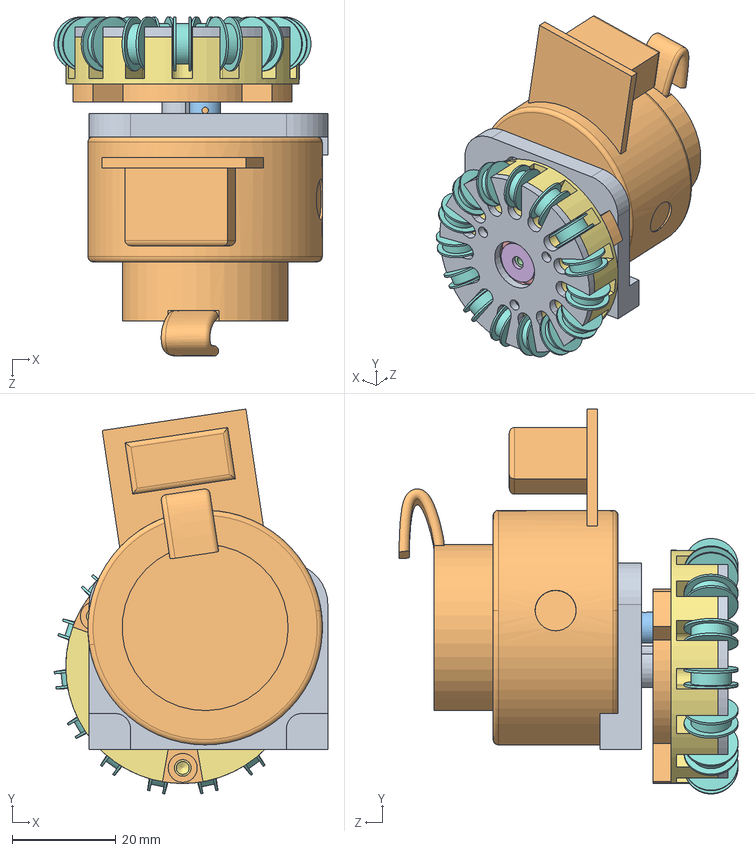
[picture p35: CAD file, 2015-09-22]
SSLv2.1/Designs/motor assembly/motor assembly.SLDASM
52.7 x 74.2 x 65.3 mm
2 motor mount
ssl_motor
4 motor gear
4 main bolt
radial ball bearing_68_am
4 washer
4 back part
60 subwheel x 15
4 front part
4 wheel gear

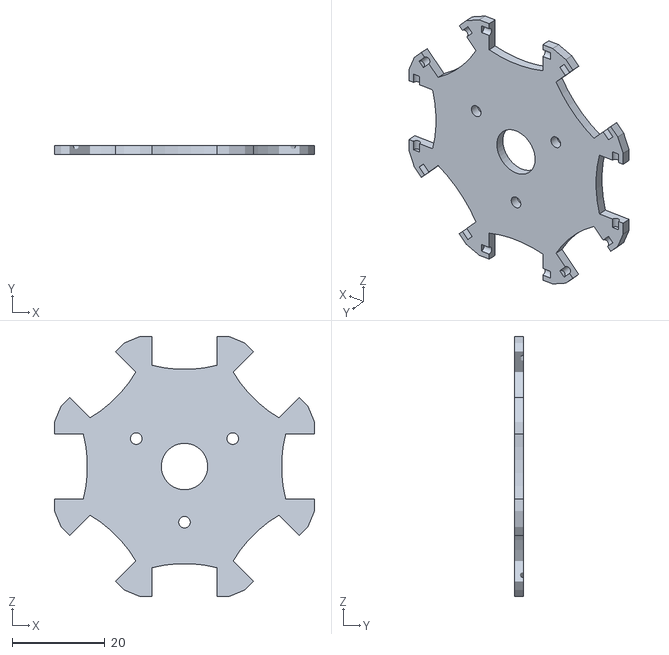
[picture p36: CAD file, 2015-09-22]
SSLv2.0/Omniwheel1/part_mainmirror.STL
56.0 x 2.00 x 56.0

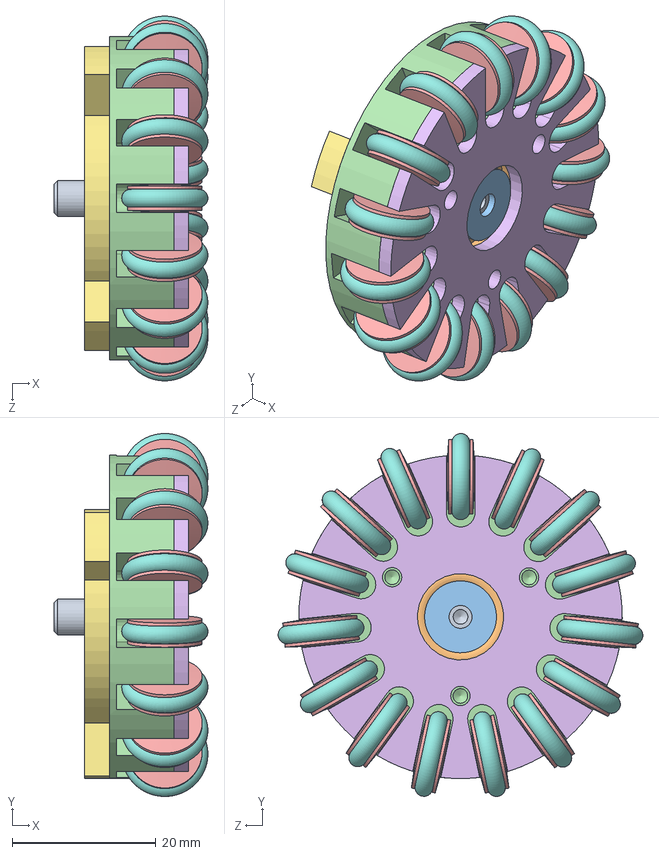
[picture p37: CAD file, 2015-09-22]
SSLv2.1/Designs/motor assembly/omniwheel/omniwheel assembly.SLDASM
21.4 x 50.5 x 50.7 mm
4 main bolt
radial ball bearing_68_am
4 washer
4 back part
60 subwheel x 15
4 front part
4 wheel gear
Sub_o-ring x 15

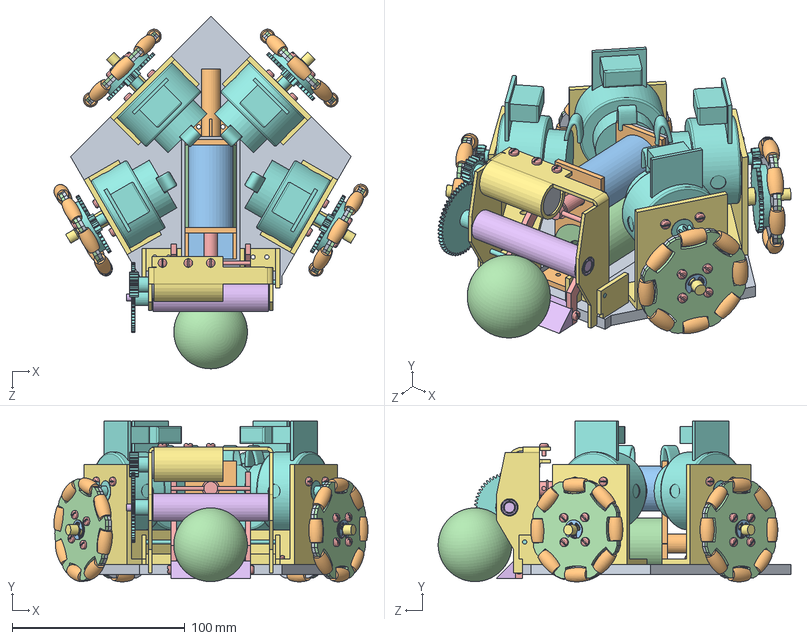
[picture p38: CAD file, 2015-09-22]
SSLv2.0/bot.SLDASM
182.0 x 93.1 x 204.4 mm
base
solenoid clamp x 2
chip solenoid
directsolnenoid
chip plunger
rod
clamp x 4
ssl motor x 4
drib motor
direct plunger
striker
ball
new arm x 2
new striker
sheet metal drib support
spur gear_am x 10
omnimain x 4
omnismall x 32
smallaxle x 32
mainmirror x 4
pan slot head_am x 35
radial ball bearing_68_am x 5
u hinge x 2
rod1 x 2
plate
e-ring external retaining ring_am x 4

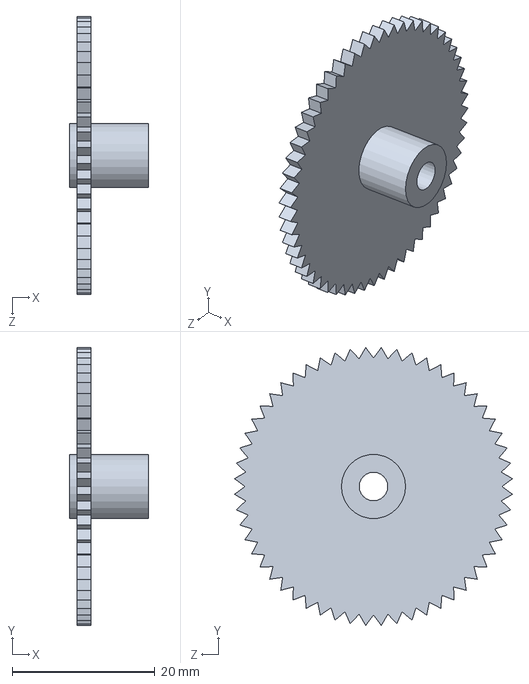
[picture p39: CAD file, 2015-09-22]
SSLv2.0/rod gear.SLDPRT
11.0 x 38.9 x 38.9 mm

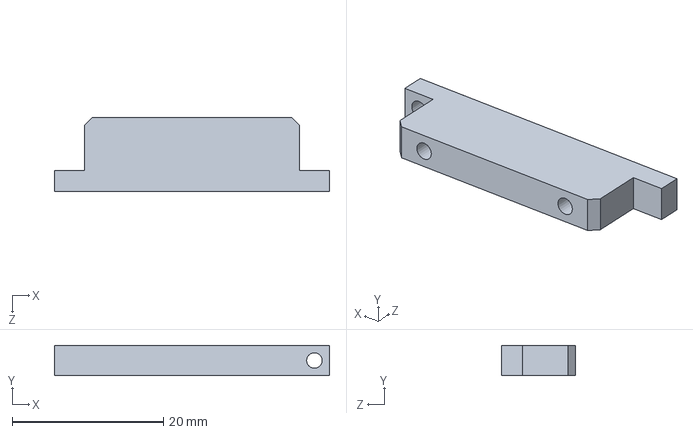
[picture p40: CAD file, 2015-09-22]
SSLv2.1/Designs/chip kicker/2 chip holder.SLDPRT
36.4 x 4.00 x 9.80 mm

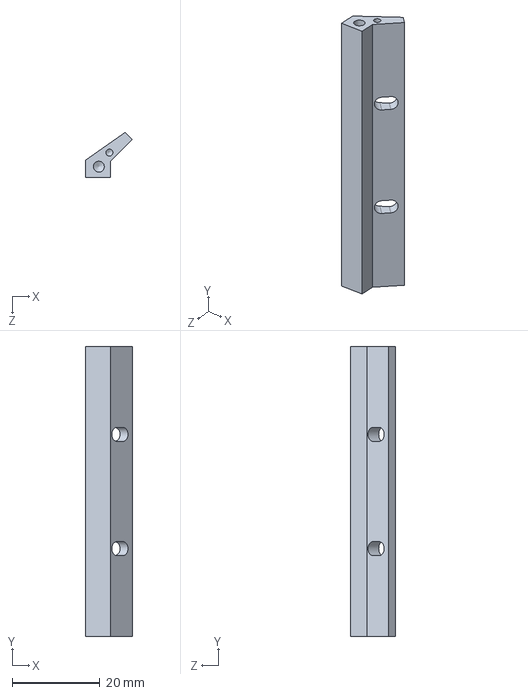
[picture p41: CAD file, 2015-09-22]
SSLv2.1/Designs/dribbler/1 dribbler support middle.SLDPRT
10.6 x 66.0 x 10.3 mm

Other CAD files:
SSLv2.0/Omniwheel1/mainmirror.SLDPRT
SSLv2.1/Designs/motor assembly/motor assembly other.SLDASM
SSLv2.0/Omniwheel1/omnimain.SLDPRT
SSLv2.1/Designs/motor assembly/ssl_motor.SLDPRT
SSLv2.0/2D drawings/Part2.SLDDRW
SSLv2.0/2D drawings/base.SLDDRW
SSLv2.0/2D drawings/chip plunger.SLDDRW
SSLv2.0/2D drawings/clamp.SLDDRW
SSLv2.0/2D drawings/new arm.SLDDRW
SSLv2.0/2D drawings/new striker.SLDDRW
SSLv2.0/2D drawings/plate.SLDDRW
SSLv2.0/2D drawings/sheet metal drib support.SLDDRW
SSLv2.0/2D drawings/solenoid clamp.SLDDRW
SSLv2.0/2D drawings/u hinge.SLDDRW
SSLv2.0/Maxon ec 16.SLDPRT
SSLv2.0/Omniwheel1/omnismall.SLDPRT
SSLv2.0/Omniwheel1/part13_subwheel.STL
SSLv2.0/Omniwheel1/part14_wheel_one_half.STL
SSLv2.0/Omniwheel1/smallaxle.SLDPRT
SSLv2.0/Part2.SLDPRT
SSLv2.0/ball.SLDPRT
SSLv2.0/base.SLDPRT
SSLv2.0/battery.SLDPRT
SSLv2.0/chip plunger.SLDPRT
SSLv2.0/chip solenoid.SLDPRT
SSLv2.0/chip1.SLDPRT
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

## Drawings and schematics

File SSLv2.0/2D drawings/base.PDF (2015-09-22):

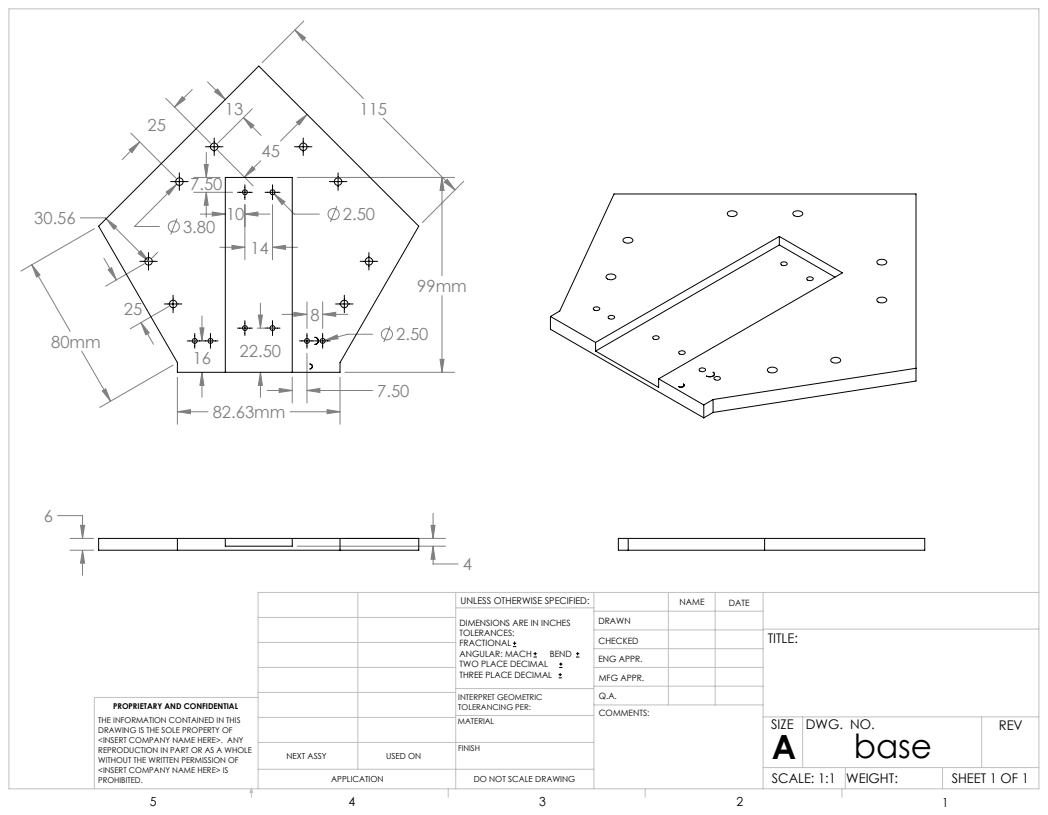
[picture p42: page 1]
SHEET 1 OF 1; SCALE: 1:1 WEIGHT:; DWG. NO.; REV; MFG APPR.; ENG APPR.; INTERPRET GEOMETRIC TOLERANCING PER:; ANGULAR: MACH; BEND; NEXT ASSY; USED ON

UNLESS OTHERWISE SPECIFIED:

DIMENSIONS ARE IN INCHES
TOLERANCES:
FRACTIONAL
TWO PLACE DECIMAL
THREE PLACE DECIMAL

PROPRIETARY AND CONFIDENTIAL
THE INFORMATION CONTAINED IN THIS
DRAWING IS THE SOLE PROPERTY OF
<INSERT COMPANY NAME HERE>. ANY
REPRODUCTION IN PART OR AS A WHOLE
WITHOUT THE WRITTEN PERMISSION OF
<INSERT COMPANY NAME HERE> IS
PROHIBITED.

DO NOT SCALE DRAWING

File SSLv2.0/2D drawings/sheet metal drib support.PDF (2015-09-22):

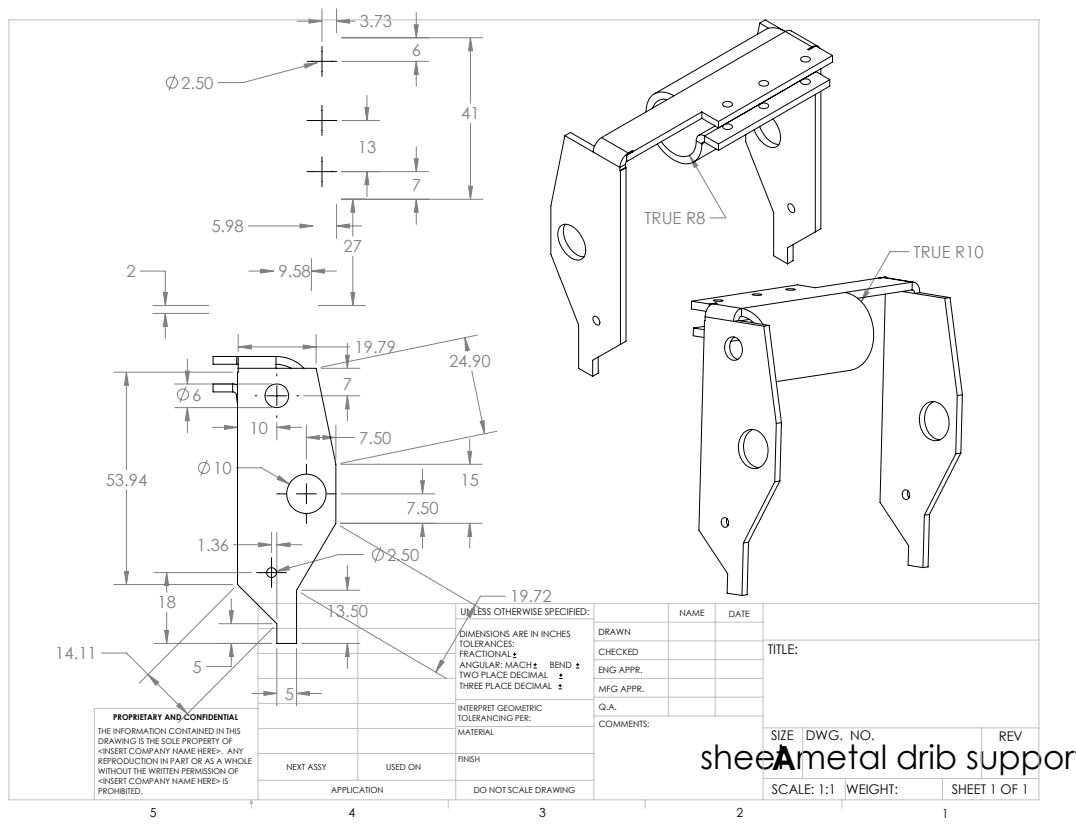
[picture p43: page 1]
TRUE R8; TRUE R10; SHEET 1 OF 1; SCALE: 1:1 WEIGHT:; DWG. NO.; REV; INTERPRET GEOMETRIC TOLERANCING PER:; ANGULAR: MACH; BEND; NEXT ASSY; USED ON

UNLESS OTHERWISE SPECIFIED:

DIMENSIONS ARE IN INCHES
TOLERANCES:
FRACTIONAL
TWO PLACE DECIMAL
THREE PLACE DECIMAL

DRAWN
CHECKED
ENG APPR.
MFG APPR.
COMMENTS:
sheet metal drib support

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

DO NOT SCALE DRAWING

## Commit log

2015-09-22 SSL v1 SW Files Added
    [Maxon ec 16.SLDPRT, Part2.SLDDRW, Part2.SLDPRT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]
2015-09-22 SSL v2 Added
    [1 chip kicker.SLDPRT, 1 chip plunger.SLDPRT, 1 chip solenoid shell.SLDPRT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]
2015-09-22 Pics Added Readme Updated
    [1 chip kicker.SLDPRT, 1 chip plunger.SLDPRT, 1 chip solenoid shell.SLDPRT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]
2015-09-22 Documentation Added
    [1 chip kicker.SLDPRT, 1 chip plunger.SLDPRT, 1 chip solenoid shell.SLDPRT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]
